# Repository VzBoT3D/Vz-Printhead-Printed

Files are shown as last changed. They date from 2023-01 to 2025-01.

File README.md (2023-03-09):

# The Vz-Printhead Printed Version

The Vz-Printhead is a light weight  and stiff head made for the VzBoTs. It was designed to be compatible with almost all hotends,
and extruders out there. With the height adjustable fan duct, you can easily change your config without having to re-print a new fan duct.

Online browser CAD : https://a360.co/41X9bWe

### If you wish to support my work, please consider a small donation at: https://ko-fi.com/vez3d

vz-Printhead Printed

## This project is licensed Non-commercial except for our authorized partners


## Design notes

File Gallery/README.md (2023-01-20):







Vz-Printhead_test_2023-Jan-16_01-28-04AM-000_CustomizedView5455202619
Vz-Printhead_test_2023-Jan-16_01-34-21AM-000_CustomizedView24598878226
Vz-Printhead_test_2023-Jan-16_01-36-20AM-000_CustomizedView21432792325
Vz-Printhead_test_2023-Jan-16_01-43-46AM-000_CustomizedView5589183573
Vz-Printhead_test_2023-Jan-16_01-46-05AM-000_CustomizedView33377179719
Vz-Printhead_test_2023-Jan-16_02-24-10AM-000_CustomizedView35012307349
Vz-Printhead_test_2023-Jan-16_02-30-41AM-000_CustomizedView5363080926

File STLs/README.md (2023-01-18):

Print settings: 
- 5 layer walls
- 4 layer bottom + top (or 5)
- 15% infill

Print Orientation:


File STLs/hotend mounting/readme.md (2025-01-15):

Hotend screw size/lengths:

Goliath/Dragon/Rapido M2.5x8mm Flathead Countersunk Bolts.

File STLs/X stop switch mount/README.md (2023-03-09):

- Option 1 is the standard [microswitch](https://s.click.aliexpress.com/e/_DesuSFL)
- Option 2 is using this [microswitch](https://s.click.aliexpress.com/e/_Dd1zqol)

BOM:

Option1:
- 2 x M3 6mm
- 2 x M2 screw

Option2:
- 4 x M3 6mm

Option1

Option2


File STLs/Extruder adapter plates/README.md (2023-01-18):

Print settings: 
- 5 layer walls
- 4 layer bottom + top (or 5)
- 15% infill


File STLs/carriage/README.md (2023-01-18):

Print settings: 
- 5 layer walls
- 4 layer bottom + top (or 5)
- 15% infill



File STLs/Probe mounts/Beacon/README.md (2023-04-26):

Beacon Sensor needs to be between 2mm and 2.6mm from the nozzle tip. So you will have to print your scalable fan duct spacer/standoffs with the correct heigh depending on your hotend


## Below are the lenght of spacers to print according to hotend. BUT, it is always best to measure with your current setup because nozzle sizes may/will be different than the cad version depending on the brand/type used. (for Vcore3 MGN9 version, substract 2.75mm)

| Hotend | Spacer lenght  |
| --- | ---- |
|Goliath long version (Goliath with it's heatsink)| 21.75mm  |
|Rapido HF|  not compatble (unless the hotend universal adapter plate is thicker to lower the hotend)|
|Rapido UHF| 15mm |
|Dragon with crazy NV volcano| not compatible (Unless you add the UHV v6 adapter (then use 16mm) or hotend universal adapter plate is thicker to lower the hotend) |
|Magnum+| 18.5mm |



BOM:
- 4 x M3 heat inserts
- 2 x M3 10mm (For rear fan duct to sliding mount)
- 2 x M3 (For brace scalable spacers lenght will vary based on your hotend)
- 2 x M3 6mm Ultra low profile (Provided in the kit)

## Probe offset:
X:0 Y:30.884



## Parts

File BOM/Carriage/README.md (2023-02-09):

| Quantity | Part | Image | comment  | Links  |
| --- | ---- | --- | ----- | -----	|
| 8 | M3 10mm Flathead counter sunk Bolts or 15mm for MGN12 version| |  Mounting top and bottom plate to standoffs | |
| 6 | M3 8mm Flathead counter sunk Bolts| | 4 for the MGN9 rail block + 2 for the cable holder | |
| 4 | M3 30mm Aluminum standoffs |   |  5mm OD | https://s.click.aliexpress.com/e/_DCGB3Sj or https://amzn.to/3ZFTbqq  |
| 17 | M3 heat insertss | |  M3x4.6x5mm (4-5mm long) (can also be 5mm OD instead of 4.5-4.6) | https://s.click.aliexpress.com/e/_De28c87 or https://amzn.to/3ZVI5xR  |



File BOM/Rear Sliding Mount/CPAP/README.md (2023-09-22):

| Quantity | Part | Image | comment  | Links  |
| --- | ---- | --- | ----- | -----	|
| 2 | M3 10mm Flathead counter sunk Bolts| | Mounting rear slider to back plate | |
| 2 | M3 nuts| | Mounting rear slider to back plate | |
| 2 | M3 6mm button head or socket head Bolts| | CPAP tube C Clamp | |
| 2 | M3 heat inserts | |  M3x4.6x5mm (4-5mm long) (can also be 5mm OD instead of 4.5-4.6) | https://s.click.aliexpress.com/e/_De28c87 or https://amzn.to/3ZVI5xR  |



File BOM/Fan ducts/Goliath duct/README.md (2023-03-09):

Goliath fan duct can be used with CPAP or 5015 fan, and other hotends long enough like Mosquito Magnum+ as long as they are at least 65mm long total.
The duct is braced to the under plate using printed spacer. Default lenght for Goliath is 15mm but can be scaled in your Slicer in Z to the desired lenght according to the hotend used

| Quantity | Part | Image | comment  | Links  |
| --- | ---- | --- | ----- | -----	|
| 2 | M3 30mm button head or socket head Bolts| | bottom plate brace | |
| 2 | M3 12mm button head or socket head Bolts| | to rear sliding mount | |
| 2 | M3 heat insertss | |  M3x4.6x5mm (4-5mm long) (can also be 5mm OD instead of 4.5-4.6) | https://s.click.aliexpress.com/e/_De28c87 or https://amzn.to/3ZVI5xR  |



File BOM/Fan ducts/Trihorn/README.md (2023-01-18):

Trihorn fan duct can be use with CPAP or 5015. It is used for shorter hotend below 65mm long total. Depending on the lenght of your hotend, you may or may not need to use the brace spacer tube. If the fan duct sits at its highest position, it can be brace without spacer just using 2xM3 12mm bolts

| Quantity | Part | Image | comment  | Links  |
| --- | ---- | --- | ----- | -----	|
| 2 | M3 12mm button head or socket head Bolts| 12mm or longer depending on the lenght of the hotend | bottom plate brace | |
| 2 | M3 12mm button head or socket head Bolts| | to rear sliding mount | |
| 2 | M3 nuts | | | |



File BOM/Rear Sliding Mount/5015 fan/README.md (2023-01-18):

| Quantity | Part | Image | comment  | Links  |
| --- | ---- | --- | ----- | -----	|
| 2 | M3 10mm Flathead counter sunk Bolts| | Mounting rear slider to back plate | |
| 2 | M3 nuts| | Mounting rear slider to back plate | |
| 2 | M3 20mm button head or socket head Bolts| | 5015 fan  | |
| 2 | M3 heat insertss | | For 5015 fan mount M3x4.6x5mm (4-5mm long) (can also be 5mm OD instead of 4.5-4.6) | https://s.click.aliexpress.com/e/_De28c87 or https://amzn.to/3ZVI5xR  |



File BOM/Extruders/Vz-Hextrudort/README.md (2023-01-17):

| Quantity | Part | Image | comment  | Links  |
| --- | ---- | --- | ----- | -----	|
| 2 | M3 8mm Flathead counter sunk Bolts| | Mounting extrduer to top plate | |

### Vz-Hextrudort mounts directly to the top plate without any adapter plate.




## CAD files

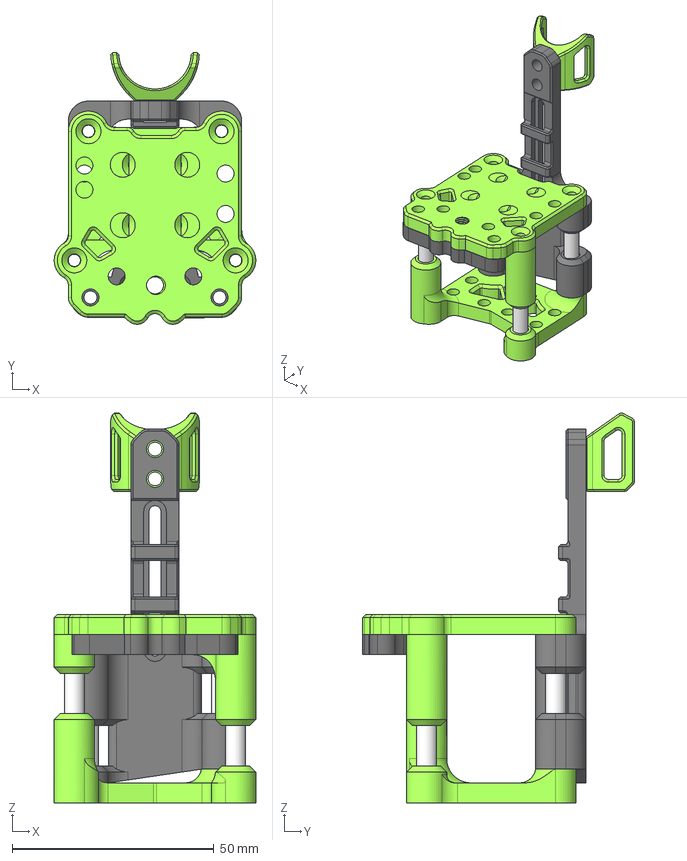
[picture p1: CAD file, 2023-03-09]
CAD/Vz-Printhead Printed RatRig MGN9.step
50.0 x 67.4 x 96.7 mm
Vz-Printed Printhead for Ratrig v1
Vz-Printed Printhead for Ratrig v1 (1)
Top MGN9H
Top MGN9C
Front
Vz-Printed Printhead for Ratrig v1 (2)
Vz-Printed Printhead for Ratrig v1 (3)
Ratrig Logo Nose
Back
Hotend universal adapter plate
Bottom\
Ratrig Logo Face
cable holder Vz (1)

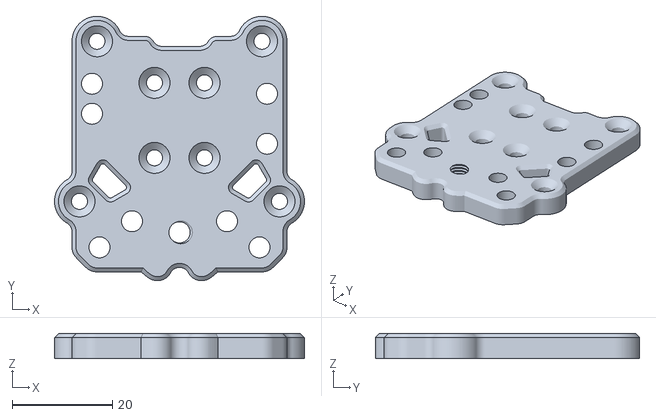
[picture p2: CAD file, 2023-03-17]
STLs/carriage/RatRig/Top MGN9C.stl
50.0 x 52.9 x 5.00

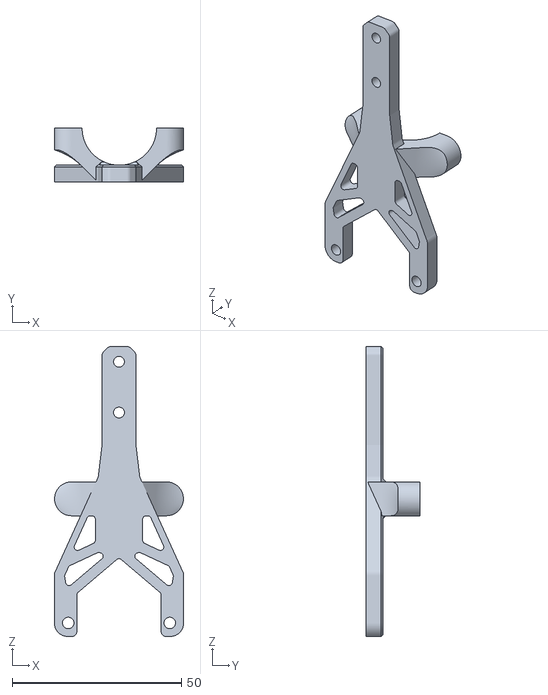
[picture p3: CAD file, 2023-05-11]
STLs/carriage/Rear sliding mount CPAP 18mm.stl
38.2 x 16.0 x 85.7

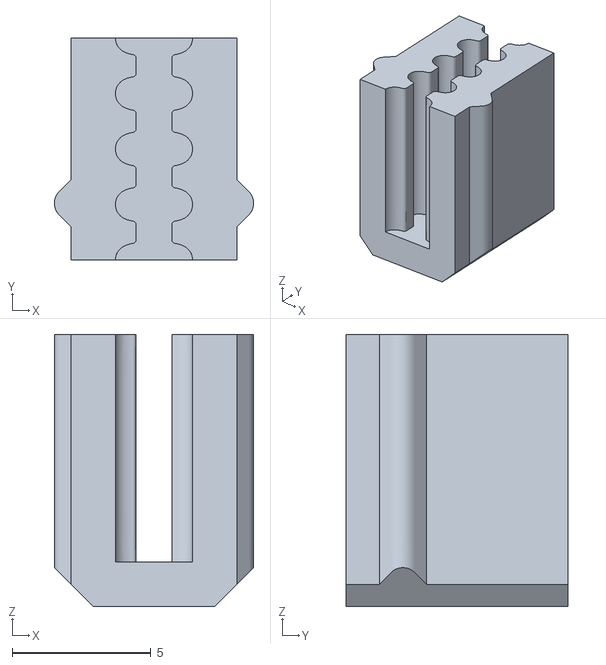
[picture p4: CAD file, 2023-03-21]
STLs/carriage/VzBoT/Belt clip-smooth idler.stl
7.18 x 8.00 x 9.80

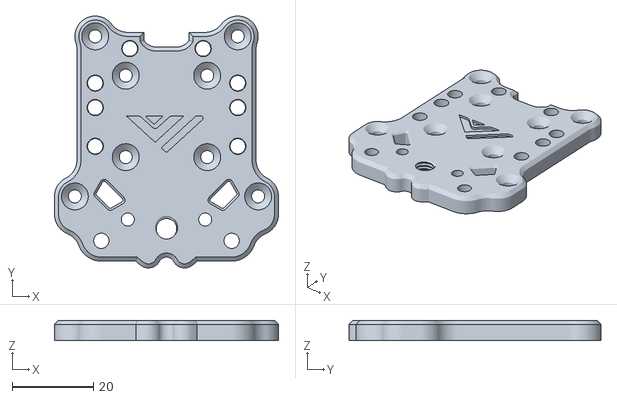
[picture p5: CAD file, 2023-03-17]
STLs/carriage/VzBoT/MGN12/Top plate MGN12H.stl
55.0 x 61.9 x 5.00

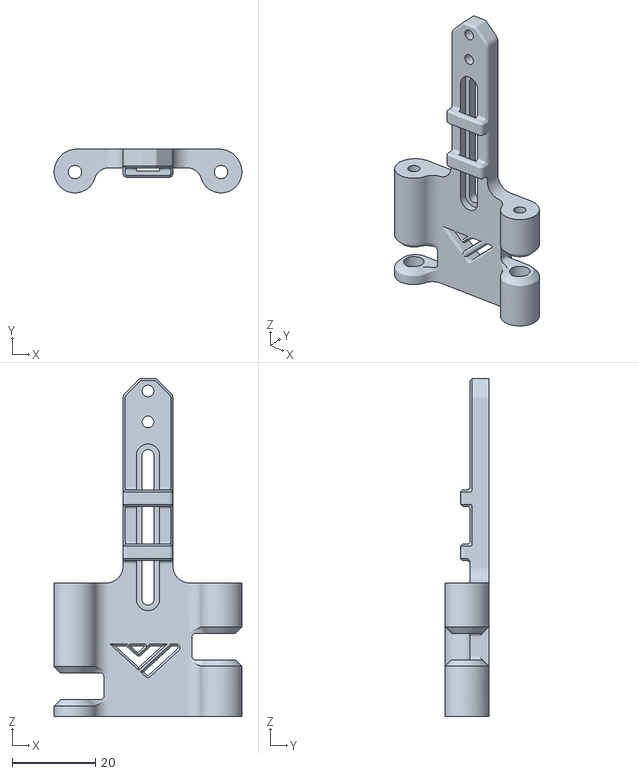
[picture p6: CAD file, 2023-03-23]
STLs/carriage/VzBoT/MGN9/Back plate round standoff.stl
45.0 x 10.5 x 81.0

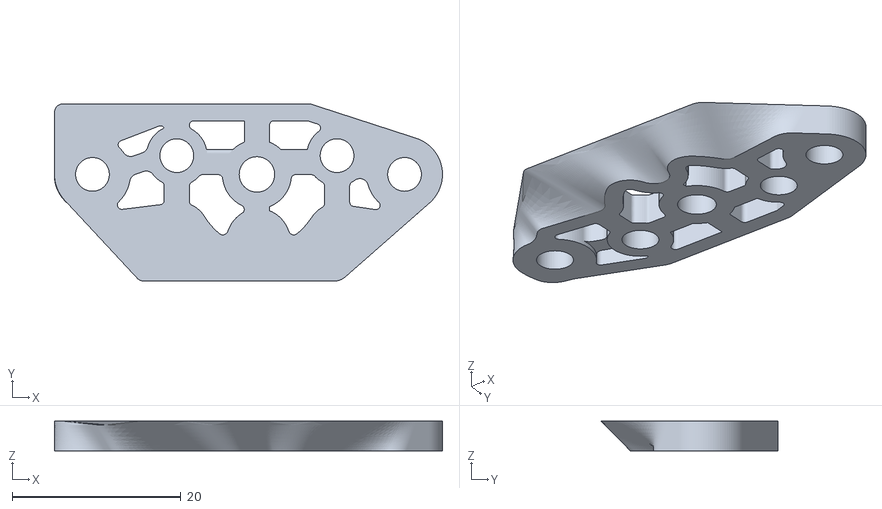
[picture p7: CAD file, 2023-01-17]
STLs/Extruder adapter plates/Orbiter v2 adapter plate.stl
46.0 x 21.0 x 3.50

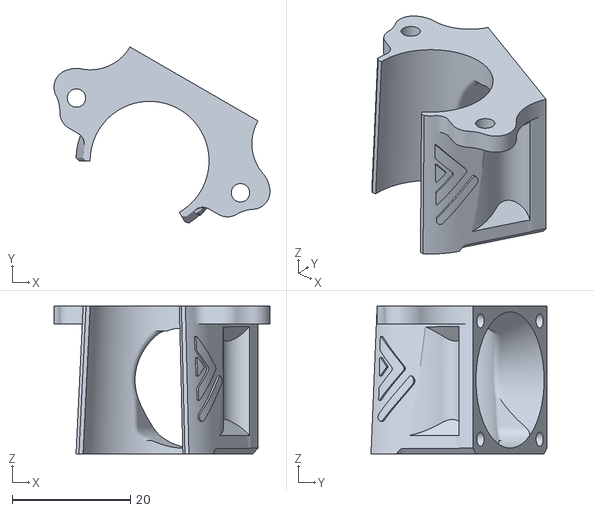
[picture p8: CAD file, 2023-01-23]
STLs/hotend heatsink fan ducts/rapido heatsink duct 2510.stl
36.5 x 29.8 x 25.0

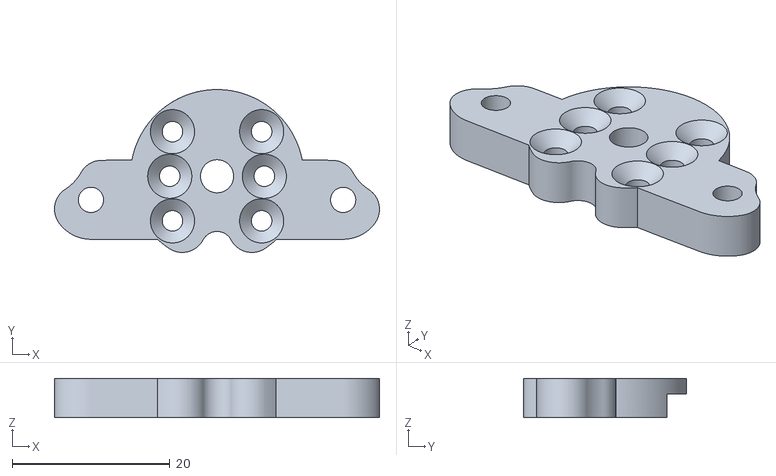
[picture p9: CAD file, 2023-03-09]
STLs/hotend mounting/Universal hotend mounting plate.stl
41.2 x 20.7 x 5.00

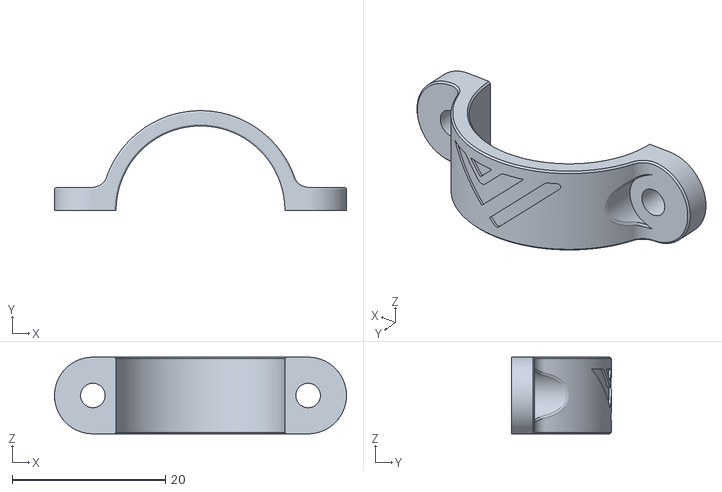
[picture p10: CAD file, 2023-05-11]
STLs/part cooling ducts/CPAP C clamp 18mm.stl
38.1 x 13.0 x 10.0

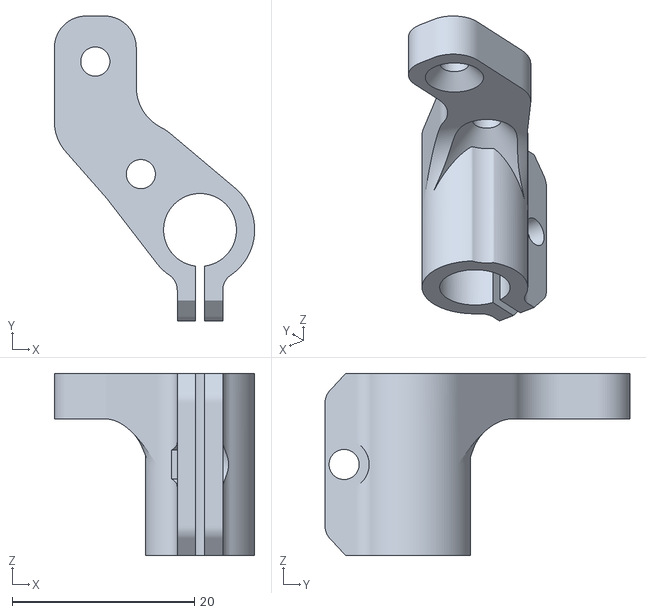
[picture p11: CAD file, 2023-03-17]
STLs/Probe mounts/8mm probe/8mm probe mount-VzBoT-MGN12.stl
22.0 x 33.5 x 20.0

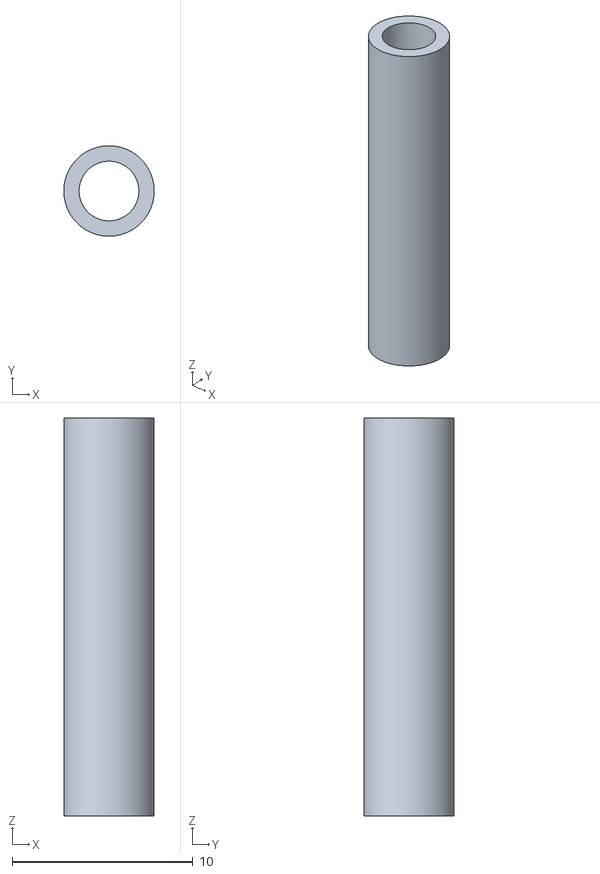
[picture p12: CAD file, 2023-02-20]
STLs/Probe mounts/Beacon/scalable spacers.stl
5.00 x 5.00 x 22.0

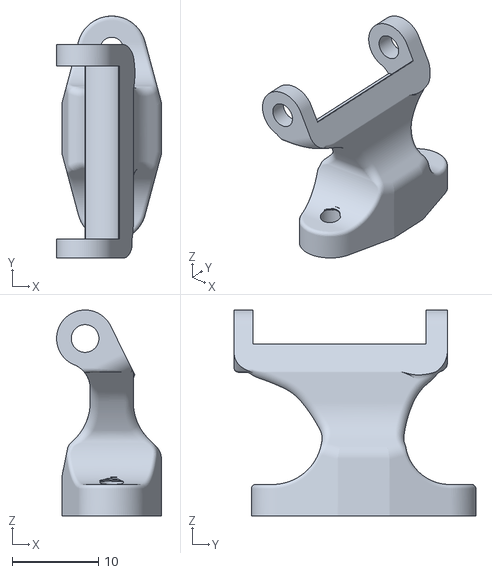
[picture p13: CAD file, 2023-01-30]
STLs/Probe mounts/BlTouch mount for 5015/BlTouch mount.stl
12.1 x 28.0 x 23.9

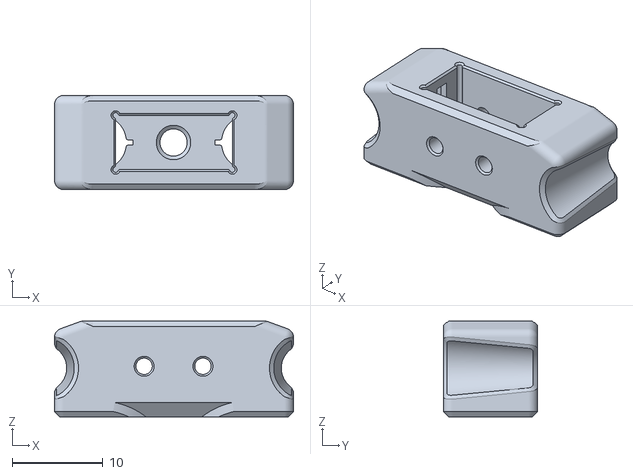
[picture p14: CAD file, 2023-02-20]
STLs/Probe mounts/QuickDraw/probe holder.stl
26.4 x 10.4 x 10.6

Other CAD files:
STLs/X stop switch mount/x stop switch mount option2.stl
STLs/carriage/RatRig/Top MGN9H.stl
STLs/carriage/Rear sliding mount 5015-Beacon.stl
STLs/carriage/VzBoT/Belt clip cover-smooth idler.stl
STLs/Extruder adapter plates/Sherpa micro adapter plate.stl
STLs/Extruder adapter plates/Sherpa mini adapter plate.stl
STLs/Probe mounts/8mm probe/8mm probe mount-VzBoT-MGN9.stl
STLs/X stop switch mount/x stop switch mount.stl
STLs/carriage/RatRig/Back.stl
STLs/carriage/RatRig/Belt Clip.stl
STLs/carriage/RatRig/Bottom.stl
STLs/carriage/RatRig/Front.stl
STLs/carriage/RatRig/Universal Hotend adapter.stl
STLs/carriage/RatRig/cable holder.stl
STLs/carriage/Rear sliding mount 5015.stl
STLs/carriage/Rear sliding mount CPAP 15mm.stl
STLs/carriage/VzBoT/Belt_clip touthed.stl
STLs/carriage/VzBoT/MGN12/Back Plate.stl
STLs/carriage/VzBoT/MGN12/Bottom Plate.stl
STLs/carriage/VzBoT/MGN12/Front.stl
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

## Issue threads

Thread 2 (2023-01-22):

MGN12 Compatibility Request

Ram-85, 2023-01-22:
Hi,

Thanks for your awesome design! Would it be possible to add MGN12 mounting holes for the top plate, or have an MGN12 version of it. I have couple printers with MGN12 that I would love to test this print head with. Thanks!

Closed 2023-02-15.

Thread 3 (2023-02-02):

Rear sliding mount 5015 missing from current cad model

mdsitton, 2023-02-02:
The original model i had:
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

current model:
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

Closed 2023-02-24.

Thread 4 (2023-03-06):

RatRig MGN9 - Belt position deviated on Y and Z axis

pedromelim, 2023-03-06:
When trying to adapt the Printhead to use on the original MGN12 Carriage from the RatTig, i discovered that the belt positioning on the Vz-Printehead Printed for the RatRig, to use the MGN9H, is off both in Y and Z axis.

I found these using as a guide the supplied V-Core 3 assembly supplied by RatRig.

Vz-PrintHead Printed RatRig MGN9

Measured from the middle of carriage

Front Posts position (Y AXIS) - 17mm
Rear Posts position (Y AXIS) - 15.8mm

Considering V-core 3 assembly and how the belt should wrap around post, position should be:

Front Posts position (Y AXIS)- 16.601mm
Rear Posts position (Y AXIS)- 15.419mm

For the belt position measured from the top of the carriage to the middle of the 9mm belt:

Top Belt position (Z AXIS) - 12.7mm
Bottom Belt position (Z AXIS) - 25.717mm

With MGN12C (Default V-Core 3 Carriage):

Top Belt position (Z AXIS) - 17.6mm
Bottom Belt position (Z AXIS) - 30.6mm

If we consider that the MGN12C does have 3mm more than the MGN9H, then the adjusted position for the Vz-PrintHead Printed RatRig MGN9 should be:

Top Belt position (Z AXIS) - 14.6mm
Bottom Belt position (Z AXIS) - 27.6mm

In summary:

Front Posts - Should be moved 0.399mm closer to the carriage
Rear Posts - Should be moved 0.381mm closer to the carriage

Top Belt Position - Should be lowered by 1.9mm
Bottom Belt Position - Should be lowered by 1.883mm

karnadii, 2023-03-06:
@pedromelim can you show an image please for the measurement deviation?

pedromelim, 2023-03-06:
> @pedromelim can you show an image please for the measurement deviation?

All i could do would be to take screenshot measuring in Fusion 360 with some extra calculations. Did not print this as iam trying to remix this for the MGN12C that RatRig includes with the V-core 3.

Would that work?

karnadii, 2023-03-06:
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

that would do.

karnadii, 2023-03-06:
Fixed, check https://www.printables.com/model/379041-ratrig-vz-printed-printhead-betauntested/files

let me know if there is another issue.

Closed 2023-03-06.

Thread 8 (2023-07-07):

Ratrig version top plate: Wrong hole diameter for extruder mounting holes

ganzgustav22, 2023-07-07:
The Ratrig version top plate seems to have M4 countersunk holes for extruder mounting instead of M3 countersunk. I think these should also be M3 on the Ratrig version, as the threads in the vz-hextrudort are M3. But it seems to be M4 in the Ratrig version.

Please see attached picture.
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

karnadii, 2023-07-07:
Hello, for fast response, please make an issue on discord on channel #vz-printhead or facebook tagging vez. No vzbot team is monitoring github issue.

ganzgustav22, 2023-07-07:
Thanks for quick reply, did that.

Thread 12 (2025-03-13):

Fan duct height from Nozzle Tip

ambarusa, 2025-03-13:
Hello,

Can you provide some values on how far the fan duct tip should be from the nozzle's tip in general? It probably depends on the angle of the duct, but in the HeroMe system, it was specified to be 0.5 mm above the nozzle's end. Is this a good reference value here as well?

Thank you

andersevenrud, 2025-03-13:
I'm also wondering about this. General recommendations online seems to be about 2-5mm, and on another printer I have the Hero Me Gen7 and the (printable) spacing tool used is ~1.6mm.

Would be nice to have some concrete official information about this.

I asked on the VzBot Discord a couple of days ago, but haven't gotten any replies. I'll post here if/when I get some answers.

ambarusa, 2025-03-13:
Hahh I used the same spacing tool. The distance looks reasonable...

andersevenrud, 2025-03-14:
I got a response on the discord. I'll just copy/paste the conversation here:

```
Anders Evenrud
 —
Hi! What's the optimal/recommended distance above the nozzle/bed for the parts cooling duct ? I have a Rapido UHF and using CPAP with the included Vz-Printhead (printed) standard duct.

strider
 —
For your Rapido UHF with the CPAP cooling setup and the Vz-Printhead (standard duct), the optimal distance of the part cooling duct from the nozzle tip is generally around 1-2mm.

Why?
Too close (below 1mm) → You risk air bouncing back onto the hotend, reducing thermal efficiency and potentially causing uneven cooling.
Too far (above 2mm) → The airflow might spread too much, losing its focused cooling effect on the print.
CPAP + Vz-Printhead Considerations:
Since CPAP setups provide high-pressure airflow, keeping it at 1-1.5mm from the nozzle ensures a concentrated flow without too much dispersion.
The Vz-Printhead duct is designed to focus air around the print, so you want to make sure it's evenly hitting all sides of the nozzle's extrusion zone.
How to Fine-Tune:
Use a Feeler Gauge or Thin Card - Slide a 1mm feeler gauge (or just a business card) between the nozzle tip and the duct. It should just clear without scraping.
Print a Cooling Test - Try thin walls, overhangs, and bridges to see if cooling is evenly distributed.
Check for Airflow Direction - The duct should direct airflow at the extrusion zone, not the heater block.
If you notice cooling issues (e.g., warping, poor overhangs), adjusting the fan speed via Klipper/firmware settings can help balance it out.
```

---

So I suppose using the Hero spacing tool is a great place to start :)

ambarusa, 2025-03-14:
Thanks very much for the effort!

Closed 2025-03-14.

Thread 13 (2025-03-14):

Place to install an ADXL345 Sensor

ambarusa, 2025-03-14:
Hello,

I would be interested if there is any convenient space to mount an accelerometer, possibly with USB-C, for example the FLY-ADXL345 board.

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

Did someone got an idea for a place?

Thanks a lot!

andersevenrud, 2025-03-21:
There's a model on printables that makes it possible to mount the Fly on the underside of the printhead, but it might not fit depending on the hotend you have (and seems to be designed for the CNC version).

https://www.printables.com/model/1013224-vzbot-adxl345-mount-aligned

It could not fit a angled USB cable on my setup using a Rapido UHF. Can't remember how much clearance I had, but might be possible to make it work if I were to butcher the cable a little bit by removing the plastic casing around the connector.

So, I used the same model and just cut away the mounting section in the slicer and screwed it down through one of the holes to the top-right. Probably not optimal location, but it sits tight and I get consistent and clean graphs.

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

ambarusa, 2025-03-24:
Hello @andersevenrud. Great idea! Can't wait to try it out. Thanks a lot for the feedback!

ambarusa, 2025-03-24:
@andersevenrud I quickly made a remix and uploaded to Printables for other builders. I used your photo to the minimum one image uploaded.
Please have a look to the stl, and let me know if I made a mistake.

https://www.printables.com/model/1241286-vzbot-adxl345-mount-on-top

andersevenrud, 2025-03-24:
> I used your photo to the minimum one image uploaded, I hope that's OK to you

No problem :)

> Please have a look to the stl, and let me know if I made a mistake.

This is exactly what I did, so looks OK to me!

andersevenrud, 2025-03-24:
Just a small note. This makes the x and y axis of the sensor run in opposite direction (according to the markings on the PCB).

To swap these in Klipper:

```
[adxl345 toolhead]
axes_map: y, x, z
```

Doesn't really matter for the values and results of resonance testing, but if you're trying to narrow down exactly where/when certain resonances or vibrations are taking place (for example with shaketune), then you might wanna do this so the axis has the correct labels.

ambarusa, 2025-03-24:
Very interesting... I see the first time this attribute: `[adxl345 toolhead]`, and I don't find anything in the documentation.

andersevenrud, 2025-03-24:
Documentation: https://www.klipper3d.org/Config_Reference.html#adxl345

The "toolhead" label is just the name I gave it.

Closed 2025-03-24.

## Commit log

2023-01-17 Adding STLs
    [Back plate.stl, Bottom plate.stl, CPAP C clamp.stl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]
2023-01-17 adding more STLs
    [CPAP C clamp.stl, Under duct scalable brace spacer.stl, dragon heatsink duct 2510.stl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]
2023-01-17 Create Vz-Printhead Printed full.zip
2023-01-17 fixed front carriage cad error
    [Front.stl]
2023-01-17 fixed front carriage part
    [Front.stl]
2023-01-17 adding X stop switch mount
    [x stop switch mount.stl]
2023-01-17 updated top plate for the under extruder screw
    went from Ultra low profile to counter sunk screw for easier sourcing
    [Top plate MGN9C.stl, Top plate MGN9H.stl]
2023-01-17 adding extruder configs
    [Orbiter v2 adapter plate.stl]
2023-01-18 Adding Quickdraw STLs
    [probe holder.stl]
2023-01-18 Update Vz-Printhead Printed full.zip
2023-01-18 fixed issue on the front carriage part
    the hole for the standoffs was not all the way through
    [Front.stl]
2023-01-18 Update to the carriage. New front, back, top plates
    Fixing a design flaw for the front part of the carriage. Had to modify top and rear plate to accommodate the fix
    [Back plate.stl, Front.stl, Top plate MGN9C.stl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]
2023-01-18 update to back plate
    more tolerance for the Standoffs, and beefed up the rear sliding mount pole
    [Back plate.stl]
2023-01-19 Update Back plate.stl
    [Back plate.stl]
2023-01-19 minor fix to backplate
    [Back plate.stl]
2023-01-20 add hex standoff mod
    [Back plate hex standoff.stl, Bottom plate hex standoff.stl, Front hex standoff.stl]
2023-01-20 Fix bottom plate hex standoff
    [Bottom plate hex standoff.stl]
2023-01-21 Fix bridge hex standoff
    [Back plate hex standoff.stl]
2023-01-21 Minor change on the back plate
    -Added a little cutout on the top of the standoff hole to make it easier to print
    [Back plate round standoff.stl, Back plate.stl, Bottom plate round standoff.stl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]
2023-01-21 missing holes
    [dragon heatsink duct 2510.stl, rapido heatsink duct 2510.stl]
2023-01-23 Update rapido heatsink duct 2510.stl
    [rapido heatsink duct 2510.stl]
2023-01-23 fix to Rapido fan duct
    [rapido heatsink duct 2510.stl]
2023-01-23 Update x stop switch mount.stl
    [x stop switch mount.stl]
2023-01-24 Correcting a minor 0.035mm error on carriage
    top, front, bottom plate updated with this minor fix. The reported issue should not have caused any issue to those who have printed it before.
    [Bottom plate hex standoff.stl, Bottom plate round standoff.stl, Front hex standoff.stl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]
2023-01-25 Create BlTouch mount.stl
    [BlTouch mount.stl]
2023-01-26 Fixed the hex standoff version size
    [Back plate hex standoff.stl, Bottom plate hex standoff.stl, Front hex standoff.stl]
2023-01-26 fix hex standoffs size
    [Back plate hex standoff.stl, Bottom plate hex standoff.stl, Front hex standoff.stl]
2023-01-26 Update Vz-Printhead Printed.zip
2023-01-30 rename to MGN9
    [BlTouch mount.stl]
2023-01-31 adding new duct stl
2023-02-01 Adding RatRig printhead
    [Back plate hex standoff.stl, Back plate round standoff.stl, Back plate.stl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]
2023-02-01 Adding the new part cooling duct + Beacon support
2023-02-02 fix in the new goliath duct for the brace location
2023-02-03 minor update to front and bottom
    fixed a fillet. Non critical change that was only cosmetic.
    [Bottom plate hex standoff.stl, Bottom plate round standoff.stl, Front hex standoff.stl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]
2023-02-09 Adding MGN12 VzBoT
    [Back Plate.stl, Bottom Plate.stl, Front.stl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]
2023-02-09 adding MGN12
    [Back plate hex standoff.stl, Back plate round standoff.stl, Bottom plate hex standoff.stl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]
2023-02-20 Create scalable spacers.stl
    [scalable spacers.stl]
2023-02-20 Update Vz-Printhead Printed VzBoT MGN9.zip
2023-02-20 adding MGN12 cad
    [Vz-Printhead Printed MGN12.step]
2023-02-21 Adding 8mm probe mount
    [8mm probe mount.stl, Bottom plate round standoff.stl]
2023-02-25 updated correct STL
2023-03-06 fix belt aligment for RatRig
    [Back plate.stl, Back.stl, Front.stl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]
2023-03-06 Updating bottom plate of ratrig version
    [Bottom plate MGN9H.stl]
2023-03-07 Update ratrig carriage STL
    [Back.stl, Bottom.stl, Front.stl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]
2023-03-09 Correcting RatRig belt path
    [Vz-Printhead Printed Ratrig.step]
2023-03-09 RatRig Printhead belt alignment fix
    -new back, front, top, bottom,
    [Back.stl, Bottom.stl, Front.stl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]
2023-03-09 Updated Vz-Printhead for VzBoT
    Fixing belt alignment issue so the head now aligns both 330 and 235 Y gantry idlers better.
    Updated parts list:
    1-top plate
    2-bottom plate
    3-Front plate
    4-universal hotend adapter plate
    5-Grove mount adapter
    6-added spacer for CPAP duct
    7-extended spacer for 5015 duct
    8-Superpinda 8mm probe mount
    [8mm probe mount.stl, Back plate hex standoff.stl, Back plate round standoff.stl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]
2023-03-09 Create x stop switch mount option2.stl
    [x stop switch mount option2.stl]
2023-03-12 updated bolts for fanduct Air Goliath
2023-03-13 update to pinda probe 8mm
    [8mm probe mount-VzBoT.stl, 8mm probe mount.stl]
2023-03-13 Update to 8mm probe/pinda and minor back plate update
    -Stronger and longer probe mount for pinda
    -back plate holes for mounting the cable holder from 2.7mm to 2.8mm. So it's easy to self tap the screw.
    [8mm probe mount-VzBoT.stl, Back plate hex standoff.stl, Back plate round standoff.stl]
2023-03-17 Revised version for MGN12 VzBoT
    fixed belt alignment
    [8mm probe mount-VzBoT-MGN12.stl, 8mm probe mount-VzBoT-MGN9.stl, 8mm probe mount-VzBoT.stl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]
2023-03-17 Fit RatRig top plate extruder holes
    extruder Holes were missing the chamfers for the counter sunk bolts
    [Top MGN9C.stl, Top MGN9H.stl]
2023-03-21 Adding smooth belt clips
    [Belt clip cover-smooth idler.stl, Belt clip-smooth idler.stl, Belt_clip touthed.stl]
2023-03-23 Adding Belts and belt clips in cad
    For both version. 235 and 330. Toothed belt clips and smooth belt clips
    [Back plate round standoff.stl, Front hex standoff.stl]
2023-03-27 Update duct spacer for CPAP-MGN12.stl
    removed the internal fins
    [duct spacer for CPAP-MGN12.stl]
2023-03-27 Update Front hex standoff.stl
    [Front hex standoff.stl]
2023-05-04 Create Rear sliding mount 5015-Beacon.stl
    [Rear sliding mount 5015-Beacon.stl]
2023-05-11 Adding Cpap 18mm tube option
    [CPAP C clamp 15mm.stl, CPAP C clamp 18mm.stl, CPAP C clamp.stl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]
2024-04-17 Update Goliath short duct Beacon.stl
    Update to fit all models including model H
2024-12-02 Update Goliath short duct Beacon.stl
    Goliath short fan duct now ok with Beacon H
2025-01-15 Create readme.md
    added screw size and length needed for different hotends.
